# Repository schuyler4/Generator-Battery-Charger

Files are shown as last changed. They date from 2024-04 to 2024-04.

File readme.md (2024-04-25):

<h1> Generator Battery Charger </h1>
<p>
This is exactly what it sounds like, it is a generator that charges a lithium-ion battery pack. The difference
between this and a just plugging a battery charger into a generator (good luck finding a good HV battery charger off the
shelf) is the regulation is full system. That is, the constant current delivery to the battery is controlled via the
throttle on the engine.  
</p>
<h3>To What Extent Does this Actually Work?</h3>
<p>
A ~150V battery pack was charged for several minutes with the system, and it appeared to regulate current fairly well. A longer test
was not done because the battery pack was not fully protected with BMS (Cowboy Charging).  
There was not excessive current into the battery pack, but there was some ripple in the current (~0.5A), so the control system did not work
perfectly, but it did seem to behave more like a current source than a voltage source. Additionally, the battery pack was made out of
reused 18650 cells which may have had a higher than normal series resistance. This may have had an effect on the behavior of the control
system. 
</p>

See [Here](https://hackaday.io/project/195765-generator-battery-charger "here") for additional documentation
<h3> Directory Structure </h3>
<ul>
<li><b>circuit_board_designs:</b> This includes all the custom circuit board designs that were made for the project.</li>
<li><b>control_program:</b> This has several revisions of the firmware that controls the whole system. This firmware is run on an Arduino Nano.</li>
<li><b>mechanical:</b> Some 3D printed mechanical interface stuff.</li>
<li><b>pictures:</b> Pictures of the setup.</li>
<li><b>system:</b> This has schematic diagrams for both the HV powertrain and the low voltage system.</li>
<li><b>test:</b> Documentation of all the testing that was done with the system and various other component testing.</li>
</ul>

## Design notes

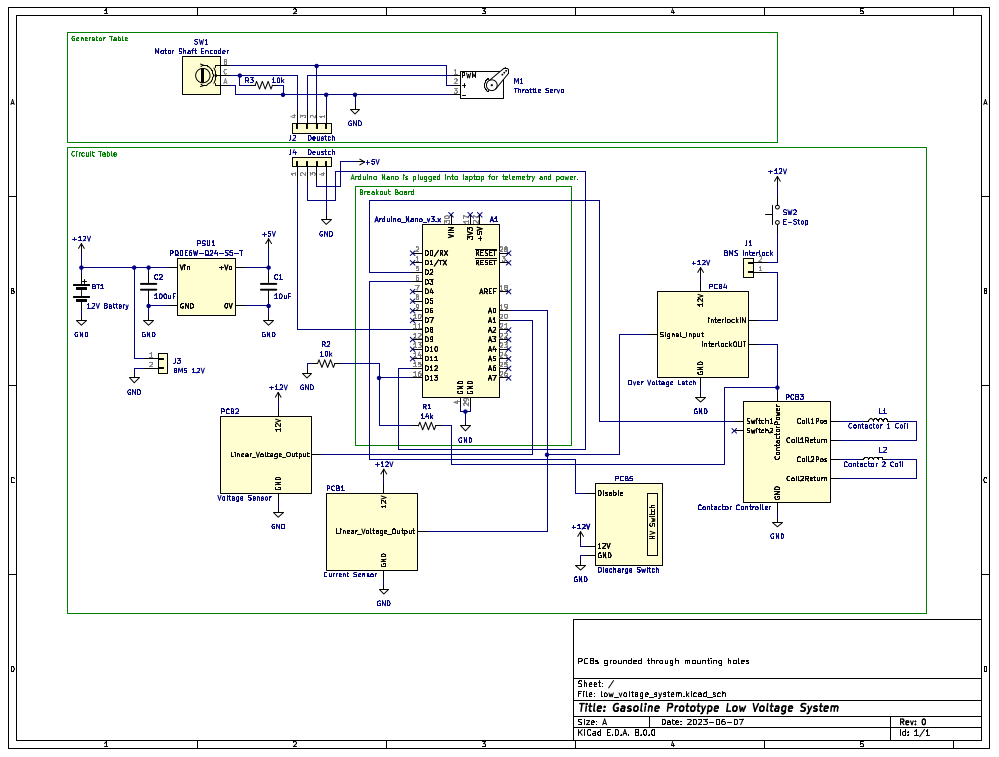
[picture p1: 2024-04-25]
pictures/low_voltage_schematic.png

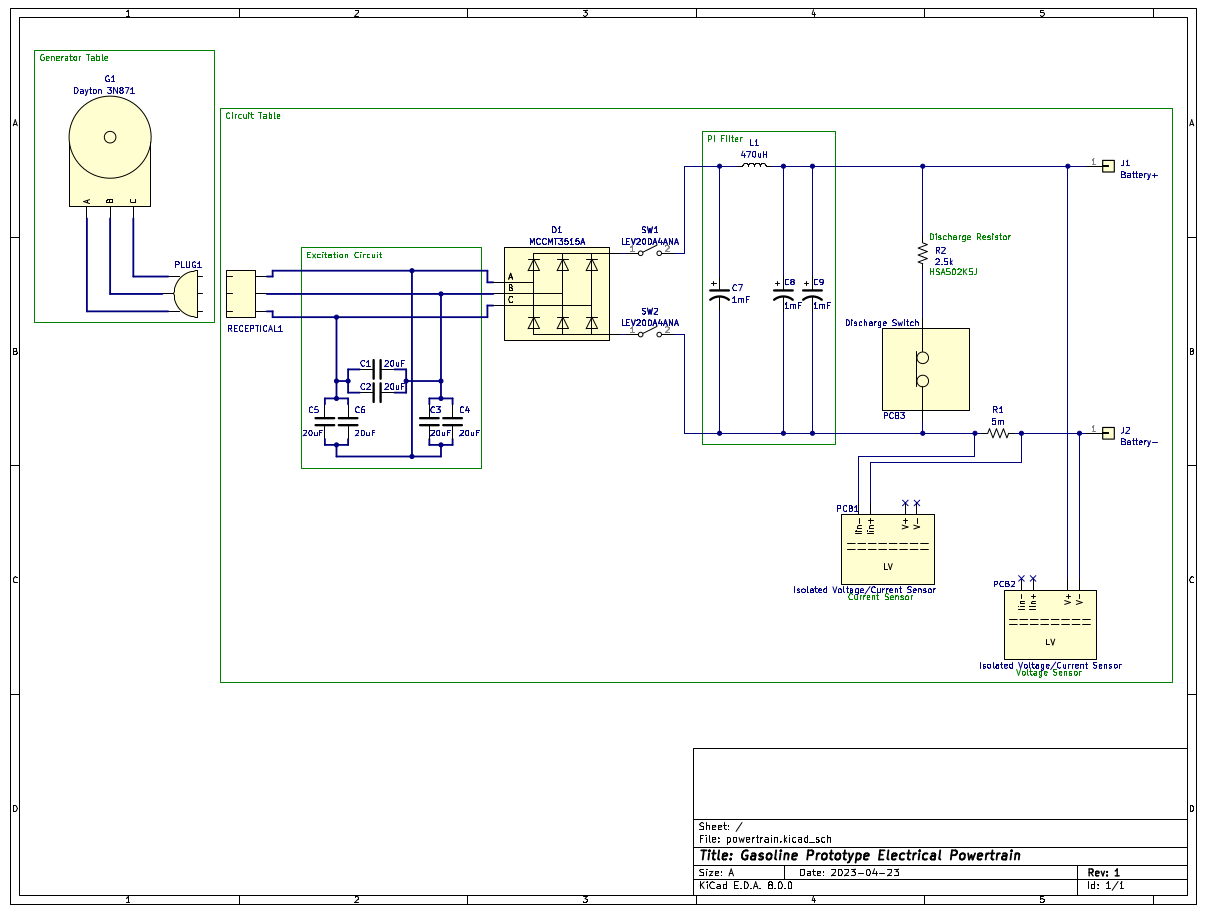
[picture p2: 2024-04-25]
pictures/powertrain_schematic.png

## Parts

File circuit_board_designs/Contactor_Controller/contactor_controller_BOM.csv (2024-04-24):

Item | Qty | Reference(s) | Value | Distributor | Distributor Part # | Unit Cost | Cost | Ordered
1 | 2 | D1, D2 | SK53A | Digikey | SK53A-LTPMSCT-ND | 0.36 | 0.72
2 | 2 | D3, D4 | SMF6.0A | Digikey | F5749CT-ND | 0.45 | 0.9
3 | 1 | J1 | Contactor Power | Digikey | 900-2125280200-ND | 1.13 | 1.13
4 | 1 | J3 | Contactor 1 Coil | Digikey | 900-2125280200-ND | 1.13 | 1.13
5 | 1 | J4 | Contactor 2 Coil | Digikey | 900-2125280200-ND | 1.13 | 1.13
6 | 1 | J5 | Switch 1 | Digikey | 900-2125280200-ND | 1.13 | 1.13
7 | 1 | J6 | Switch 2 | Digikey | 900-2125280200-ND | 1.13 | 1.13
8 | 2 | Q1, Q2 | DMG3418L | Digikey | DMG3418L-7DICT-ND | 0.43 | 0.86
9 | 2 | R1, R2 | 1k | Digikey | 311-1KMCT-ND | 0.1 | 0.2
10 | 2 | R3, R4 | 10k | Digikey | RNCP0805FTD10K0CT-ND | 0.1 | 0.2
 |  |  |  |  |  |  | 8.53

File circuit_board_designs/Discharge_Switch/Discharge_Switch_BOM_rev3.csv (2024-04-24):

Item | Qty | Reference(s) | Value | Manufacturer Part # | Distributor | Distributor Part # | Unit Cost | Cost | Carted
1 | 1 | D1 | 1N4148W | 1N4148W | Digikey | 1655-1N4148WCT-ND | 0.13 | 0.13
2 | 1 | D2 | SMF13A | SMF13A | Digikey | F5815CT-ND | 0.47 | 0.47
3 | 1 | D3 | SMF6.0A | SMF6.0A | Digikey | F5749CT-ND | 0.45 | 0.45
4 | 1 | J1 | Resistor | 212528-0200 | Digikey | 900-2125280200-ND | 1.13 | 1.13
5 | 1 | J2 | Return | 212528-0200 | Digikey | 900-2125280200-ND | 1.13 | 1.13
6 | 1 | J3 | 12V Power | 212528-0200 | Digikey | 900-2125280200-ND | 1.13 | 1.13
7 | 1 | J4 | Disable | 212528-0200 | Digikey | 900-2125280200-ND | 1.13 | 1.13
8 | 1 | K1 | DBR71205-HR | DBR71205-HR | Digikey | 725-DBR71205-HR-ND | 46.88 | 46.88
9 | 1 | Q1 | DMG3418L | DMG3418L-7 | Digikey | DMG3418L-7DICT-ND | 0.41 | 0.41
10 | 1 | R1 | 10k | RNCP0805FTD10K0 | Digikey | RNCP0805FTD10K0CT-ND | 0.1 | 0.1
11 | 1 | R2 | 1k | RNCP0805FTD1K00 | Digikey | RNCP0805FTD1K00CT-ND | 0.1 | 0.1
Total: |  |  |  |  |  |  |  | 53.06

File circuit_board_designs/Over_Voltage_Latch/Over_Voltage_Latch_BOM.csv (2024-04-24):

Item | Qty | Reference(s) | Value | Footprint | Manufacturer Part # | Distributor | Distributor Part # | Unit Cost | Cost | Carted
1 | 3 | C1, C2, C3 | 0.1uF | C_0805_2012Metric | 08055D104KAT2A | Digikey | 478-12790-1-ND | 0.1 | 0.3
2 | 1 | D1 | 1N4148W | D_SOD-123 | 1N4148W | Digikey | 1655-1N4148WCT-ND | 0.13 | 0.13
3 | 1 | D2 | SMF6.0A | D_SOD-123F | SMF6.0A | Digikey | F5749CT-ND | 0.45 | 0.45
4 | 1 | D3 | SMF13A | D_SOD-123F | SMF13A | Digikey | F5815CT-ND | 0.47 | 0.47
5 | 1 | J1 | 12V Power | MOLEX_2125280200 | 212528-0200 | Digikey | 900-2125280200-ND | 1.13 | 1.13
6 | 1 | J2 | Signal Input | MOLEX_2125280200 | 212528-0200 | Digikey | 900-2125280200-ND | 1.13 | 1.13
7 | 1 | J3 | Interlock Passthrough | MOLEX_2125280200 | 212528-0200 | Digikey | 900-2125280200-ND | 1.13 | 1.13
8 | 1 | K1 | G5Q-1A | Relay_SPST_Omron-G5Q-1A | G5Q-1A4 DC12 | Digikey | Z223-ND | 1.63 | 1.63
9 | 2 | R1, R4 | 1k | R_0805_2012Metric | RNCP0805FTD1K00 | Digikey | RNCP0805FTD1K00CT-ND | 0.1 | 0.2
10 | 4 | R3, R5, R6, R7 | 10k | R_0805_2012Metric | RNCP0805FTD10K0 | Digikey | RNCP0805FTD10K0CT-ND | 0.1 | 0.4
11 | 1 | RV1 | 10k | Potentiometer_Bourns_3266W | 3266W-1-103LF | Digikey | 3266W-103LF-ND | 4.2 | 4.2
12 | 1 | U1 | LM311 | SOIC-8_3.9x4.9mm_P1.27mm | LM311D | Digikey | 497-19620-ND | 0.67 | 0.67
13 | 1 | U2 | LM4040DBZ-2.5 | SOT-23 | LM4040C25FTA | Digikey | LM4040C25FCT-ND | 0.57 | 0.57
14 | 2 | TP1, TP2 | TestPoint | TestPointLoop_1.8mm | 1038 | Digikey | 36-1038-ND | 0.25 | 0.5
15 | 1 | U3 | NE555D | SOIC-8_3.9x4.9mm_P1.27mm | NE555DR | Digikey | 296-6501-1-ND | 0.44 | 0.44
Total: |  |  |  |  |  |  |  |  | 13.35

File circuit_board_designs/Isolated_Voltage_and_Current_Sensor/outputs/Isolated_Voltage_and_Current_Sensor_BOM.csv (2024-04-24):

Item | Qty | Reference(s) | Value | Manufacturer Part # | Mouser Part # | Unit Price | Price | Carted
1 | 1 | C1 | 1nF | CL21B102KBANFNC | 187-CL21B102KBANFNC | 0.1 | 0.1
2 | 7 | C2, C3, C4, C5, C6, C7, C10 | 0.1uF | 08055D104KAT2A | 581-08055D104K | 0.1 | 0.7
3 | 1 | C8 | 100pF | 0805B101M250CT | 791-0805B101M250CT | 0.1 | 0.1
4 | 1 | C9 | 2.2uF | CL21B225KOFNNNG | 187-CL21B225KOFNNNG | 0.12 | 0.12
5 | 1 | C11 | 10uF | CL21B106KOQNFNE | 187-CL21B106KOQNFNE | 0.23 | 0.23
6 | 2 | D1, D3 | SMF6.0A | SMF6.0A | 576-SMF6.0A | 0.46 | 0.92
7 | 1 | D2 | SMF13A | SMF13A | 637-SMF13A | 0.87 | 0.87
8 | 1 | F1 | 200mA | F0805B0R25FSTR | 581-F0805B0R25FSTR | 0.54 | 0.54
9 | 1 | J1 | Input HV | 212528-0200 | 538-212528-0200 | 0.88 | 0.88
10 | 1 | J2 | 12V Power | 212528-0200 | 538-212528-0200 | 0.88 | 0.88
11 | 1 | J3 | Linear Voltage Output | 212528-0200 | 538-212528-0200 | 0.88 | 0.88
12 | 1 | J4 | Input Current | 212528-0200 | 538-212528-0200 | 0.88 | 0.88
13 | 1 | PS1 | PDSE1-S12-S5-M | PDSE1-S12-S5-M | 490-PDSE1-S12-S5-M | 3.39 | 3.39
14 | 5 | R1, R15, R16, R13, R14 | 374k | CR0805-FX-3743ELF | 652-CR0805FX-3743ELF | 0.1 | 0.5
15 | 4 | R2, R10, R11, R12 | 100 | RMCF0805FT100R | 708-RMCF0805FT100R | 0.1 | 0.4
16 | 4 | R3, R4, R5, R6 | 1k | RMCF0805FT1K00 | 708-RMCF0805FT1K00 | 0.1 | 0.4
17 | 2 | R7, R8 | 15k | RMCF0805FT15K0 | 708-RMCF0805FT15K0 | 0.11 | 0.22
18 | 1 | U1 | AMC1100DUB | AMC1100DUB | 595-AMC1100DUB | 6.21 | 6.21
19 | 1 | U2 | L7805 | L7805ACD2T-TR | 511-L7805ACD2T-TR | 1.08 | 1.08
20 | 1 | U3 | OPA196xDBV | TS507CLT | 511-TS507CLT | 2.14 | 2.14
21 | 1 | R17 | 0 | CR0805AJ/-000EAS | 652-CR0805AJ/-000EAS | 0.1 | 0.1
total: |  |  |  |  |  |  | 21.54

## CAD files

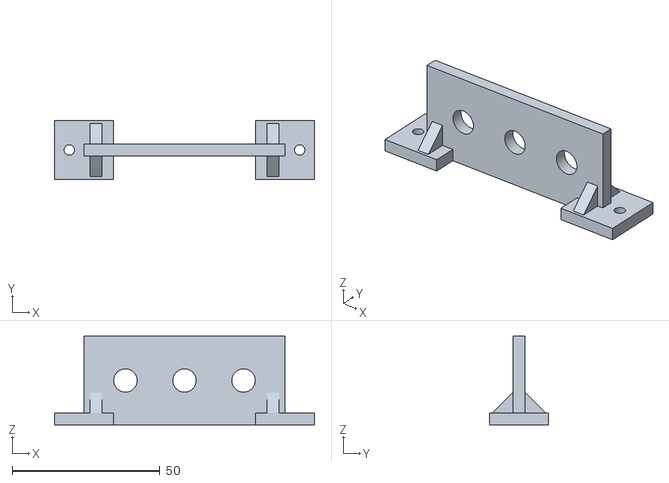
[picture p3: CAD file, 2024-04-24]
mechanical/phase_reciever/Phase_Reciever.stl
88.0 x 20.0 x 30.0

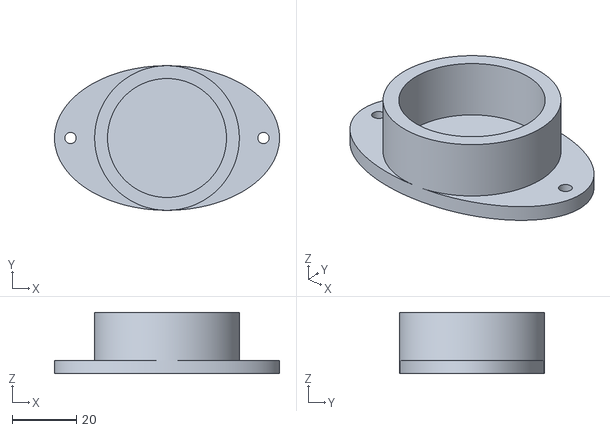
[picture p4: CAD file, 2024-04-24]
mechanical/pi_holder/inductor_holder.stl
70.0 x 45.0 x 19.0

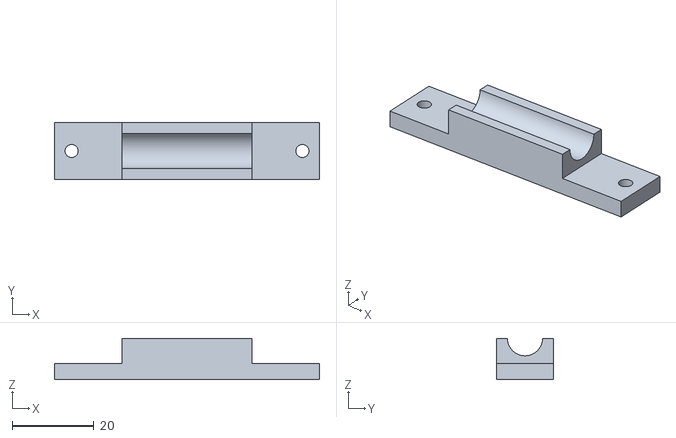
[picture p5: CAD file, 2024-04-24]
mechanical/shunt_holder/Shunt_Resistor_Holder_Bottom.stl
65.0 x 14.0 x 10.2

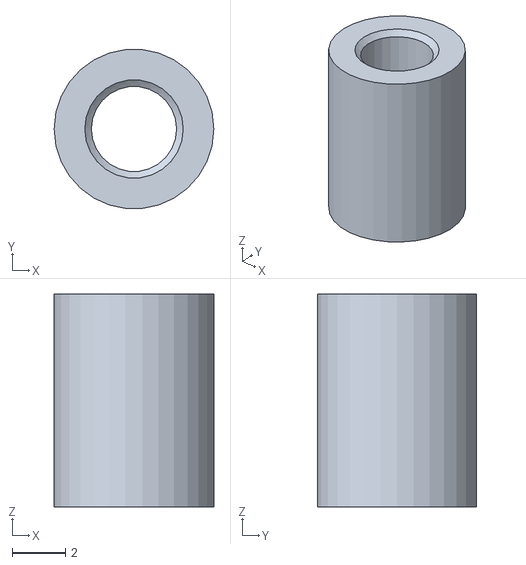
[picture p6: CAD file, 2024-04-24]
mechanical/stand_off/M3_stand_off-Body.stl
6.00 x 5.97 x 8.00

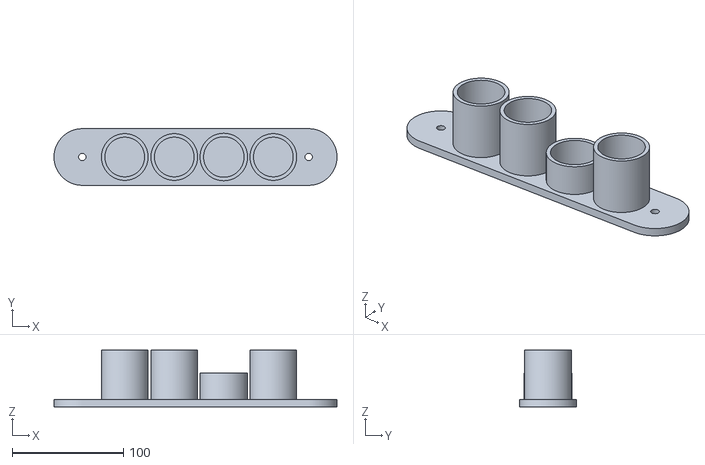
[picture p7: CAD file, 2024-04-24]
mechanical/pi_holder/PI_Holder.stl
254.0 x 50.8 x 50.8

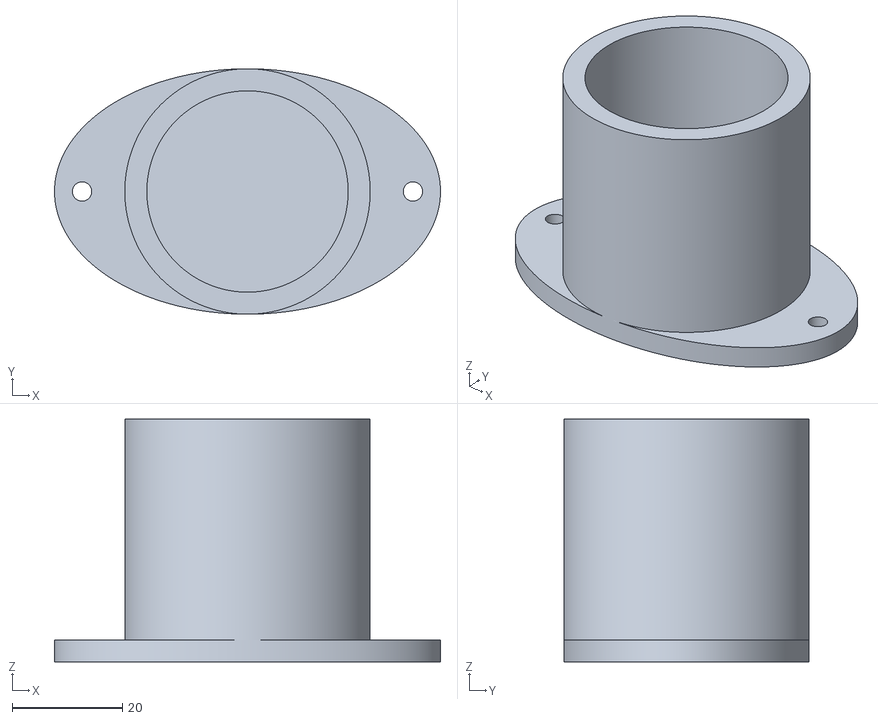
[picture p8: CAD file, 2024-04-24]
mechanical/pi_holder/capacitor_holder.stl
70.0 x 44.5 x 44.0

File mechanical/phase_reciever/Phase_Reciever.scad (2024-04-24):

module PhaseReciever()
{
    thickness = 4;
    width = 68;
    height = 30;
    
    hole_distance = 20;
    
    plug_hole_size = 7.9;
    
    curve_resolution=1000;
    
    fastener_hole_size = 3.5;
    
    foot_size = 20;
    
    gantrey_offset = 30;
    
    difference()
    {
        cube([width, thickness, height], center=true);
        
        for(i = [-1:1])
        {
            translate([i*hole_distance, 0, 0])
            rotate([90, 0, 0])
            cylinder(
                h=thickness+1, 
                center=true,
                d=plug_hole_size,
                $fn=curve_resolution);
        }
    }
    
    difference()
    {
        for(i = [-1:1])
        {
            if(i != 0)
            {
                translate([i*width/2, 0, -height/2 + 2])
                cube(
                    [foot_size, foot_size, thickness], 
                    center=true);
            }   
        }
        for(i = [-1:1])
        {
            if(i != 0)
            {
                translate([i*((width/2)+5), 0, -height/2 + 2])
                cylinder(
                    h=thickness+1, 
                    d=fastener_hole_size,
                    $fn=1000,
                    center=true);
            }
        }
    }  
    
    for(i = [-1:1])
    {
        if(i != 0)
        {
            translate([i*gantrey_offset,0,-2])
            rotate([-90,0,90])
            linear_extrude(height=thickness, center=true)
            polygon(points=[[0,0], [10,10], [0,10]]);
            
            translate([i*gantrey_offset,0,-2])
            rotate([-90,0,-90])
            linear_extrude(height=thickness, center=true)
            polygon(points=[[0,0], [10,10], [0,10]]);
        }
    }
}

PhaseReciever();

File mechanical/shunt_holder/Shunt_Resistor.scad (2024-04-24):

module ShuntResistor()
{
    cylinder_resolution = 1000;
    
    resistor_rotation = [90, 0, 0];
    resistor_length = 23.24;
    
    resistor_color = "SaddleBrown";
    
    lead_length = 10;
    lead_radius = 1.5;
    
    lead_color = "LightGrey";
    
    rotate(resistor_rotation)
    {
        color(resistor_color, 1.0)
        cylinder(
            h=resistor_length,
            r=4.17,
            center=true,
            $fn=cylinder_resolution );
        
        color(lead_color, 1.0)
        cylinder(
            h=resistor_length + 2*lead_length, 
            r=lead_radius, 
            center=true, 
            $fn=cylinder_resolution );
    }
}

     

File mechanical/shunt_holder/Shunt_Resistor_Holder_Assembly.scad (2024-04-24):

use <Shunt_Resistor.scad>
use <Shunt_Resistor_Holder_Bottom.scad>

rotate([0,0,90])
translate([0,0,8])
ShuntResistor();
ShuntResistorHolderBottom();

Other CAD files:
mechanical/shunt_holder/Shunt_Resistor_Holder_Bottom.scad

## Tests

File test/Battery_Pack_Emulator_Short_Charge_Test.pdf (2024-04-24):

Battery Pack Emulator Short Charge Test (7/27/2023)
Firmware Rev: 4
Purpose: This is the first charging test that is done with the battery pack emulator. The emulator contains 12 series cells that are monitored by a BMS as well as 36 reverse series zener diodes which are intended to emulate more cells. The voltage current characteristic of a zener diode should be similar to that of a battery that is sinking power. That is, approximately flat at a certain voltage, not linear like a resistor.
Description: The charger is set to a charge set point of 50. This corresponds to a current of 0.396A. The charger is set to this low of a current in an attempt to not burn up the zener diodes. The battery pack emulator is attached across the output of the charger and a short charge spurt is run.
Results: The charge test was terminated when some smoke was observed in the vicinity of the zener diodes. Hopefully, this was from the wood or electrical tape contacting the diodes and not the diodes themselves. The current through the battery emulator initially overshot at about 0.6A; however it then seemed to settle to about to about 0.34A to 0.38A. Before the test, the real 12s battery pack was measured at 37.93V. After the test this voltage rose to 38.35V. The following trace was recorded for the total voltage across the battery pack emulator.

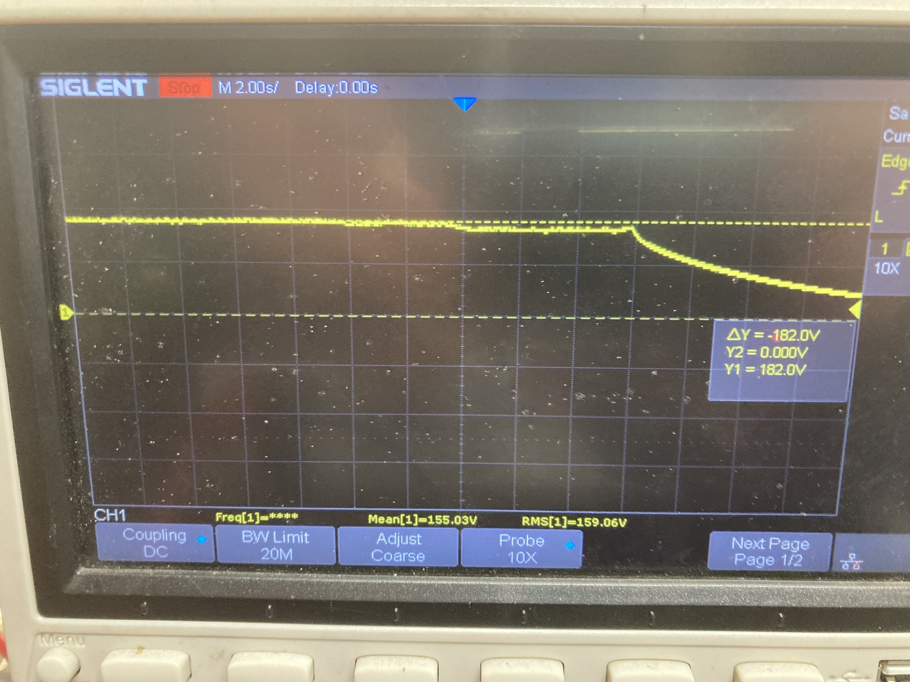
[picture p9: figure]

Analysis: The charge seemed to work as intended besides the smoke. As has been previously observed, the system does not maintain a perfect constant current. However, it regulates the current well enough to charge the batteries. That is, it acts more like a current source than a voltage source. The voltage per zener diode corresponds to approximately 4V which seems slightly high as the zener diodes are rated at 3.9V reverse voltage. This means that for future complete charge tests, the charge complete voltage threshold should be set at 193.2V or slightly lower.

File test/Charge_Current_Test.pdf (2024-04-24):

Charge Current Test (5/21/2023)
Firmware Rev: 3
Purpose: This test makes sure there are no excessive currents while charging and quantifies other charging current parameters.
Description: The test battery pack is charged with the charger system for two short spurts. During each charging spurt, the output signal of the current sensor is logged with an oscilloscope. Like the initial charge test, the test battery pack is being cowboy charged, so the pack cannot be charged for long. The parameters are found by using the horizontal cursors on the oscilloscope.
Results:
Parameter | Current Sensor Signal (V) | Measured Current (A)
Spurt 1 Average | 0.44 | 1.49
Spurt 1 Maximum | 0.56 | 1.9
Spurt 2 Average | 0.312 | 1.05
Spurt 2 Current Ripple | 0.128 | 0.42
Spurt 2 Maximum | 0.436 | 1.48
Spurt 2 Minimum | 0.164 | 0.54

Analysis: As has previously been observed, the system acts more like a constant current source than a constant voltage source; however, the current does tend to fluctuate. Additionally, a large amount of higher frequency ripple current is observed. It is possible that some of this ripple amplitude is due to noise.

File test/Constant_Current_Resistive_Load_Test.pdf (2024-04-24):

Constant Current Resistive Load Test (5/3/2023)
Purpose: Before attempting to charge a battery, it makes sense to test the constant current regulation ability of the generator charger system with a nonvolatile load.
Description: A control program is written that reads from the isolated current sensor and creates a feedback loop to regulate the current. A 250Ω load is attached across the output of the generator system, and the current set point is tested at several values. The theoretical current at the set point is calculated, and the actual current is measured using a hall effect multimeter.
Results:
ADC Code Set Point | Theoretical Current (A) | Measured Current (A) | Calculated Average Voltage (V)
120 | 0.98 | 1.04 | 260
100 | 0.815 | 0.87 | 217.5
75 | 0.605 | 0.74 | 185
An ADC set point of 50 was also attempted. This set point was not regulated in a stable manor. Analysis: The generator system seems to regulate with more stability and accuracy at higher voltages: approximately 150V-275V. The first test battery pack for charging should be in this voltage range.

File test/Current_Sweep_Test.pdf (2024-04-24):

Current Sweep Test (5/3/2023)
Purpose: This test is done to visualize and find the full range of current from the prototype generator into a 250 ohm load. It is also done to test the isolated voltage and current sensor when it is integrated into the system.
Description: First, the generator is brought to max RPM using the throttle servo control. The current is measured with the in-system current sensor and with a multimeter current sensor. Next, the generator is swept from min throttle to max throttle and the current is logged from the system current sensor and plotted using python. The data is logged using a serial transmission from the controller and Teraterm. Results:
Table 1: Comparison of in system current sensor to hall effect multimeter
Max Current Measured with in System Sensor (A) | Current Measured With Meter (A)
1.15 | 1.2

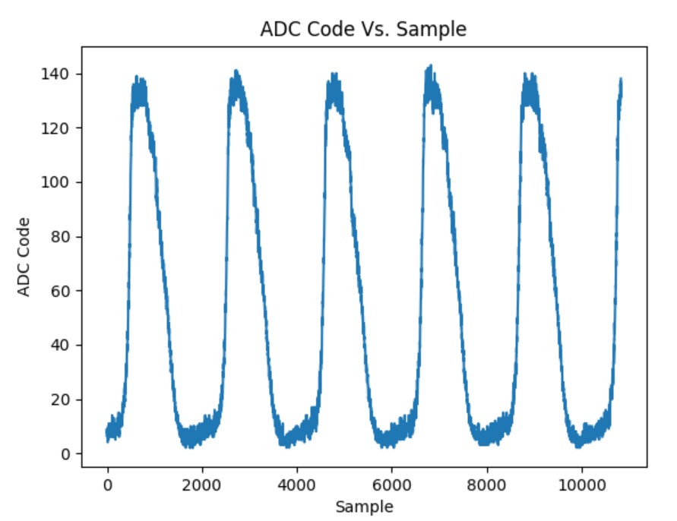
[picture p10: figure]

Figure 1: Plot of the ADC code over time

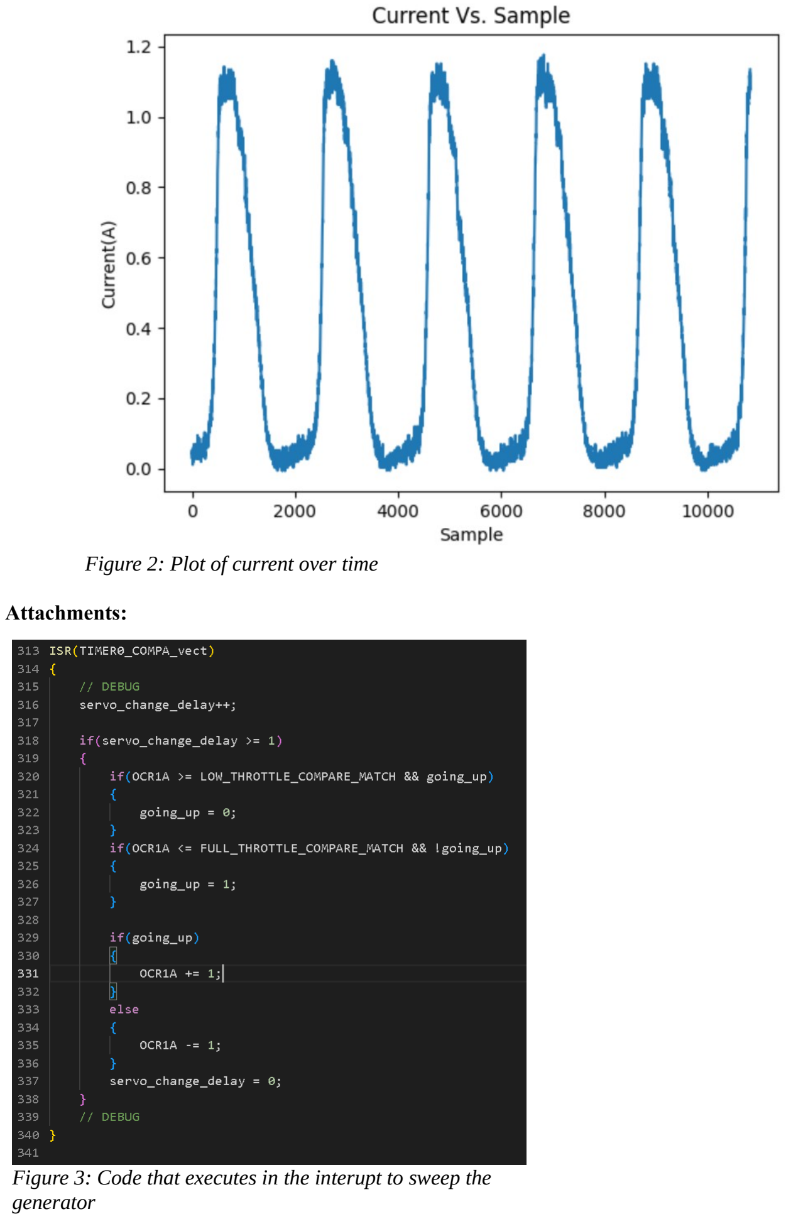
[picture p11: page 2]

Attachments:

Figure 3: Code that executes in the interupt to sweep the generator

Figure 2: Plot of current over time

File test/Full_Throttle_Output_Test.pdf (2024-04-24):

Full Throttle Output Test (7/19/2023)
Firmware Rev: 4
Purpose: This tests the maximum open circuit output voltage of the system, the accuracy of the voltage sensor, and the load regulation of the system.
Description: The system is put in full throttle test mode. This disables voltage control of the system and voltage level monitoring. Once in charge mode the open circuit output voltage is measured using an oscilloscope and the built in voltage sensor. Next, a 250Ω step load is applied and the voltage is measured using both methods again.
Results:

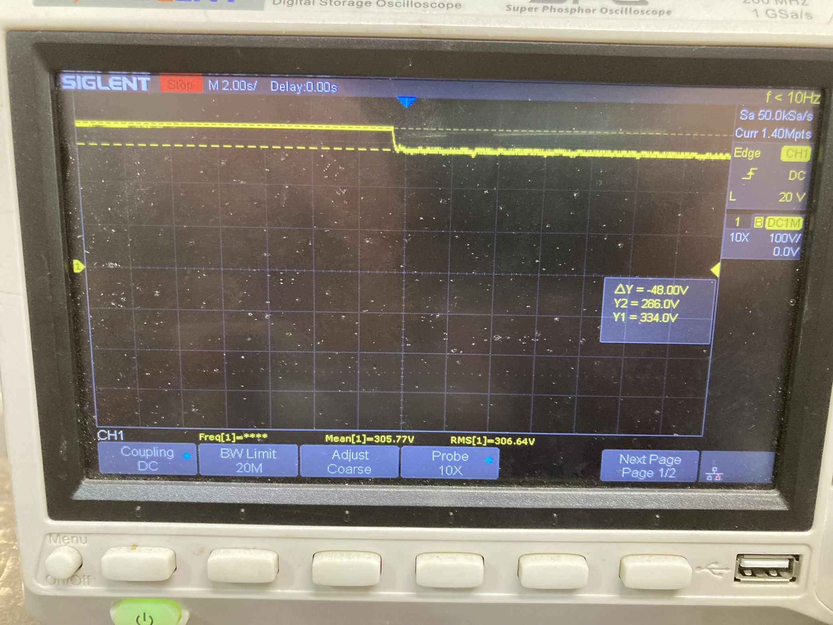
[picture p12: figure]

| Open Circuit | 250Ω Load
Oscilloscope (V) | 334 | 286
Voltage Sensor ADC Code | 472 | 408
Voltage Sensor (V) | 326.3 | 282.3
Error (%) | 2.3 | 1.3
The output power when the 250 ohm load is connected is 327W and the voltage drop when the 250Ω load is connected is 48V.
Analysis: The actual measured transfer function must be used to obtain an accurate result from the voltage sensor. That is, the theoretical transfer function cannot be used.

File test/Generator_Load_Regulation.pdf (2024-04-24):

Generator Load Regulation (5/4/2023)
Purpose: The purpose of this test is to see how much the output voltage of the generator varies just from changing the load.
Description: The induction generator with excitation capacitors is spun using a Dayton 6K748A motor. Presumably at around 3450RPM as this is the max RPM of the motor. Note that this is not necessarily a constant rotation source; it likely slows down as its load torque increases affecting the results of the test. Several resistive loads are attached across the output of the generator and the resulting output current and voltage is measured.
Results:
Load Resistance (Ω) | Current (A) | Output Voltage (V)
250 | 1.23 | 313
333 | 0.94 | 319.7
500 | 0.6 | 327
1000 | 0.3 | 332.5

Analysis: The output voltage seems to decrease approximately linearly with increaseing load current.

0.2 | 0.4 | 0.6 | 0.8 | 1 | 1.2 | 1.4

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
Output Voltage vs. Load Current

Output Voltage (V)

Current (A)

Output Voltage (V)

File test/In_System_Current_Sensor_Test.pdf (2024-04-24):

In System Current Sensor Test (5/15/2023)
Firmware Rev: 1
Purpose: The current sensor seemed to give wrong values on the last full system test. The current sensor should be tested while integrated into the system as much as possible.
Description: A power supply is attached across the shunt to supply a known current through it. The sensor output voltage is measured and recorded at various currents. Also at various currents, the ADC code that corresponds to the current that the system is reading is recorded. Both values are compared to their theoretical counterparts.
Results:
PSU Current(A) | Sensor Output Voltage (V) | Logged ADC Code
0.2 | 0.067 | 26
0.5 | 0.151 | 61
0.8 | 0.235 | 96
1 | 0.29 | 117
1.2 | 0.347 | 141
1.5 | 0.43 | 177
1.8 | 0.514 | 211
2 | 0.57 | 233
Theoretical Sensor Voltage (V) | Theoretical ADC Code | Sensor Error (%) | ADC Error (%)
0.06 | 24 | 11.67 | 8.33
0.15 | 61 | 0.67 | 0
0.24 | 98 | 2.08 | 2.04
0.3 | 122 | 3.33 | 4.1
0.36 | 147 | 3.61 | 4.08
0.45 | 184 | 4.44 | 3.8
0.54 | 221 | 4.81 | 4.52
0.6 | 245 | 5 | 4.9
0 | 0.5 | 1 | 1.5 | 2 | 2.5

0

0.1

0.2

0.3

0.4

0.5

0.6

Sensor Output Voltage Transfer Function

Sensor Output Voltage (V)

Current (A)

Sensor Output Voltage (V)

Analysis: The current sensor still seems to be functioning correctly in the system. Both the current sensor output, and the ADC code representing current that is read by the controller, seem to maintain linearity. For both parameters, the error is less than or equal to 5% except for the lowest value. The lowest value is not a usual current for the system, and the high error could also be due to the power supply sourcing the current.

0 | 0.5 | 1 | 1.5 | 2 | 2.5

0

50

100

150

200

250

ADC Code Transfer Function

Logged ADC Code

Current (A)

A

D

C

Code

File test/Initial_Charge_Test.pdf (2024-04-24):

Initial Charge Test (5/20/2023)
Firmware Rev: 3
Purpose: This is the first test where the generator system is used to put current through a battery pack to charge it.
Description: The test battery pack is attached across the output of the charger generator system. The current set point is 110. The generator is turned on, and the battery is charged. The battery pack voltage is logged using an oscilloscope, and a hall effect current sensor is also used to measure the current through the battery pack. Two short spurts of charging were done. The system is cowboy charging, so a long charging test cannot be done.
Results: The battery pack did not explode. The current that was read bounced around anywhere from 0.7A to 1A. The measured battery pack voltage before any charging took place was 151.6V, and the measured pack voltage after all the charging was 164.4V.

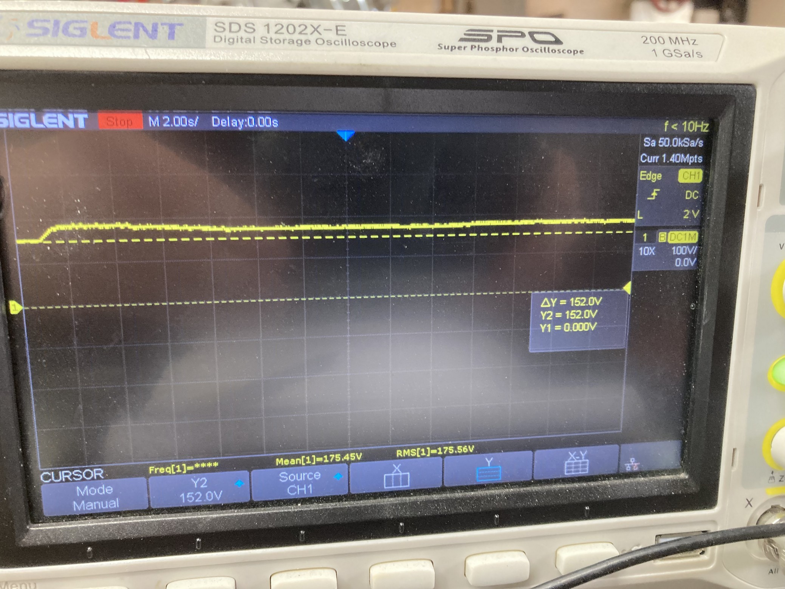
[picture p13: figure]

Figure 1: First Charging Spurt

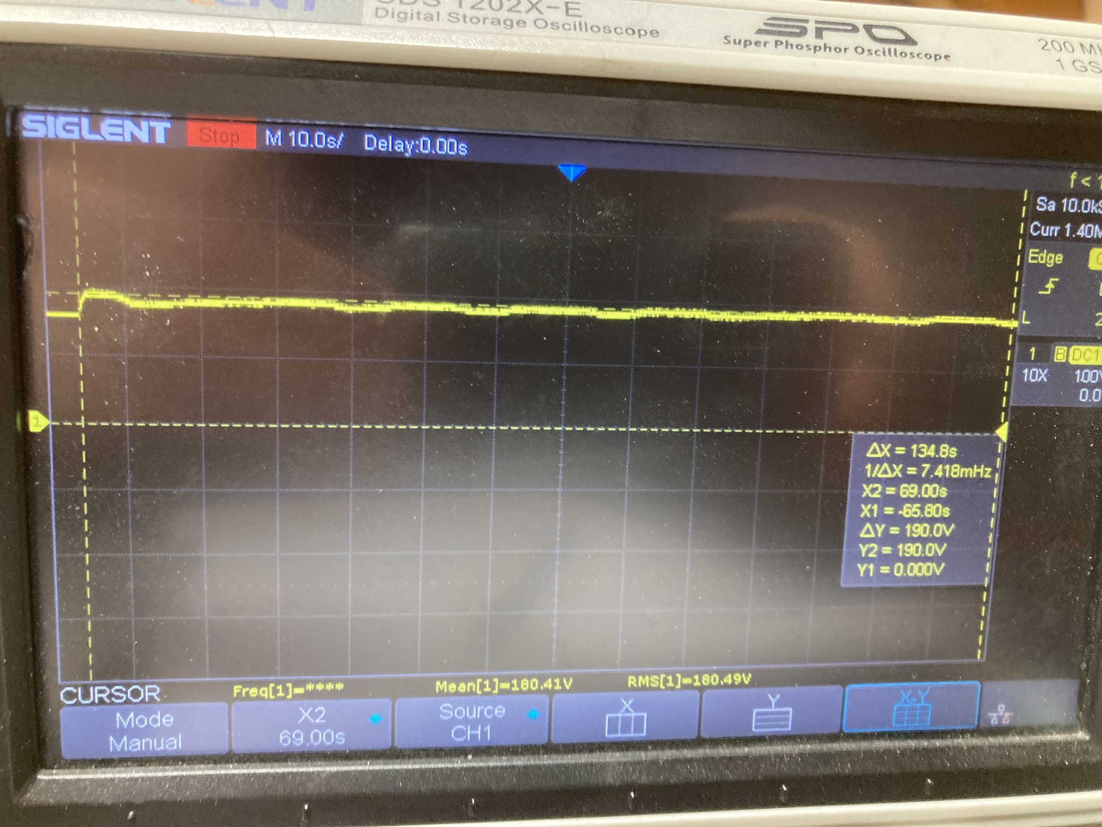
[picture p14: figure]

Analysis: The system does seem to be regulating the current to the extent required; however; the current is not completely constant and tends to bounce around. As has previously been observed, the battery voltage seems to increase more than normal at the start of charge. This is a possible indicator of poor cell health.

Figure 2: Second Charging Spurt

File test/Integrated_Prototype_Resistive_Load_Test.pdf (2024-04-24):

Integrated Prototype Resistive Load Test (7/19/2023)
Firmware Rev: 4
Purpose: This is a rerun of the resistive load test with all the electronics integrated into the prototype. The resistive load test verifies the control system can control a constant current without connecting a battery load.
Description: The charger is set to resistive load test mode. This allows the set point of the charger to be selected from three options. Each option is tested into a 250Ω resistive load. The current sensor measured ADC code is recorded and the current is also measured with a hall effect multimeter. Results:
ADC Code Set Point | Current Set Point (A)(1) | Measured ADC Code | Measured Current (A) | Calculated Voltage (V)(2)
120 | 0.983 | 119 | 0.96 | 240
100 | 0.816 | 101 | 0.83 | 207.5
75 | 0.606 | 73 | 0.65 | 162.5
(1) The current set point is computed using the current sensor transfer function.
(2) The voltage is calculated by multiplying the measured current by 250Ω.
Analysis: As was previously observed, the measured current seems to be closer to the set point for the higher voltage conditions.

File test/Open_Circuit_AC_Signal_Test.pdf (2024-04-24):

Open Circuit AC Signal Test (6/3/2023)
Purpose: This test quantifies the maximum frequency and voltage of the AC signals coming of the generator for analysis and component specifying.
Description: The generator is run with no load connected to the rectifier, with the engine set to full throttle. The voltage across each parallel set of generator excitation capacitors is measured with an oscilloscope. This measures the voltage of each phase.
Results:
Phase | Measured Peak Voltage(V) | RMS Voltage (V) | Frequency (Hz)
Phase 1 | 384 | 271.5 | 54.35
Phase 2 | 384 | 271.5 | 53.76
Phase 3 | 364 | 257.4 | 53.76
Analysis: Wiring and connectors that are used to couple these signals should be rated for at least 280VAC.
Attached Oscilloscope Captures:

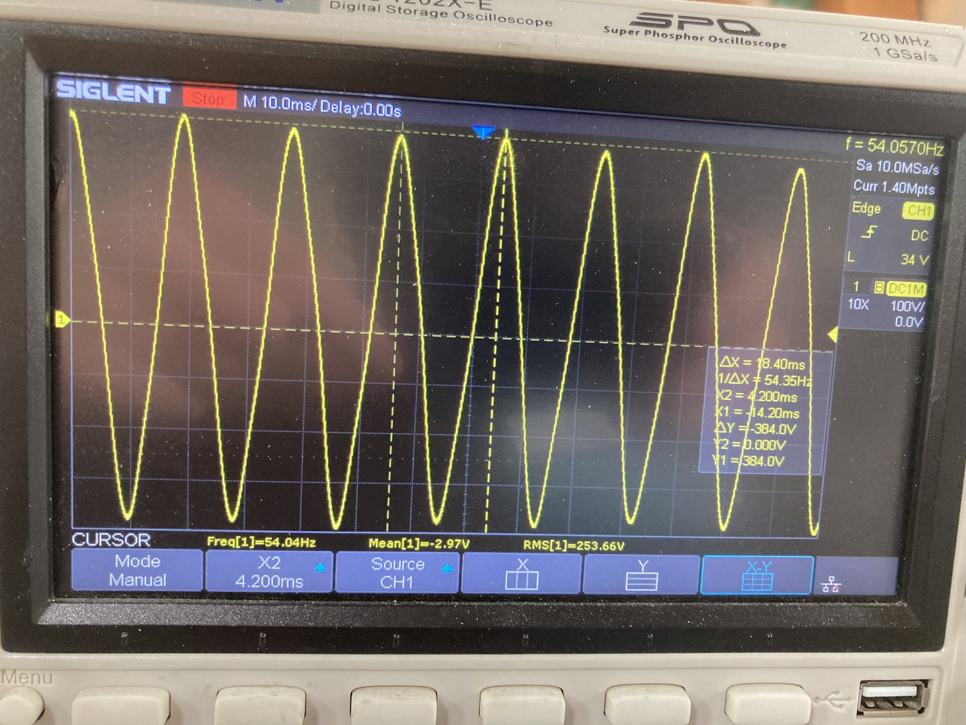
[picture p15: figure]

Figure 1: Phase 1

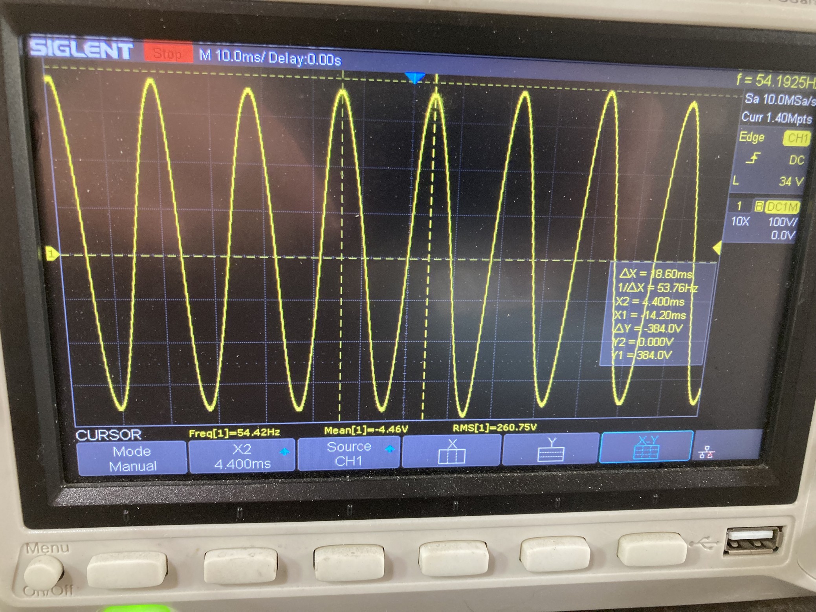
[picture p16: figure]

Figure 2: Phase2

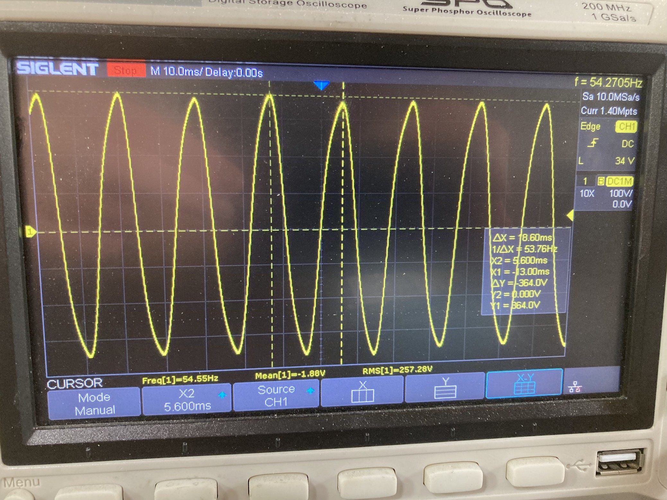
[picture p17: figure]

Figure 3: Phase3

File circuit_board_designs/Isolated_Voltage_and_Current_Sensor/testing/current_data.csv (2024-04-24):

Current (A) | Output Voltage(V)
0 | 0.01
0.5 | 0.156
1 | 0.296
1.5 | 0.447
2 | 0.586
2.5 | 0.739
3 | 0.88
3.5 | 1.023
4 | 1.167
4.5 | 1.308
5 | 1.467
5.5 | 1.604
6 | 1.754
6.5 | 1.893
7 | 2.046
7.5 | 2.184
8 | 2.337
8.5 | 2.492
9 | 2.63

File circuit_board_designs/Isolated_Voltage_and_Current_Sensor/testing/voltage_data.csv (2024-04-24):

Input (V) | Output (V)
0 | 0.01
4.967 | 0.026
10 | 0.042
15.23 | 0.058
20.07 | 0.073
25.05 | 0.089
30.08 | 0.105
338.5 | 1.077
33.52 | 0.117
100.5 | 0.309
161.7 | 0.517
194.2 | 0.629
232.9 | 0.744
259.9 | 0.824
318.2 | 1.014
290.7 | 0.927

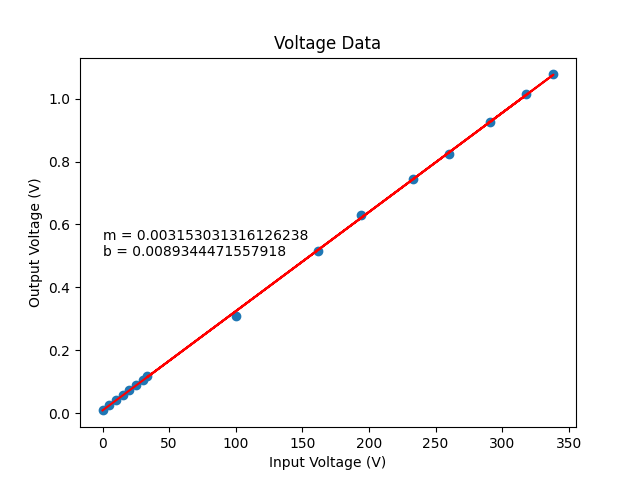
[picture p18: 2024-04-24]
circuit_board_designs/Isolated_Voltage_and_Current_Sensor/testing/plots/voltage_transfer_function.png

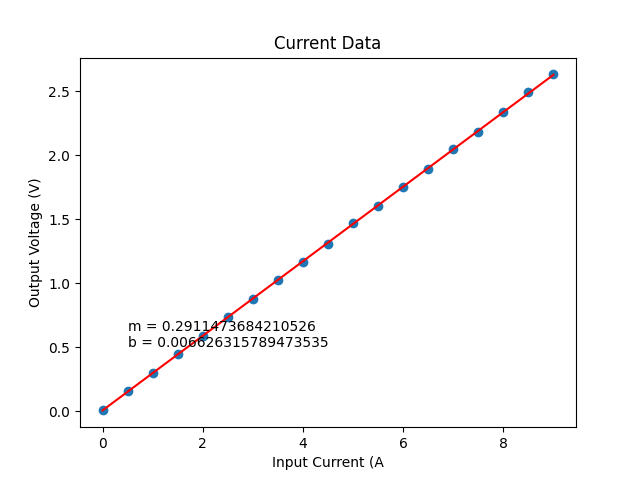
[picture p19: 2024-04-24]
circuit_board_designs/Isolated_Voltage_and_Current_Sensor/testing/plots/current_transfer_function.png

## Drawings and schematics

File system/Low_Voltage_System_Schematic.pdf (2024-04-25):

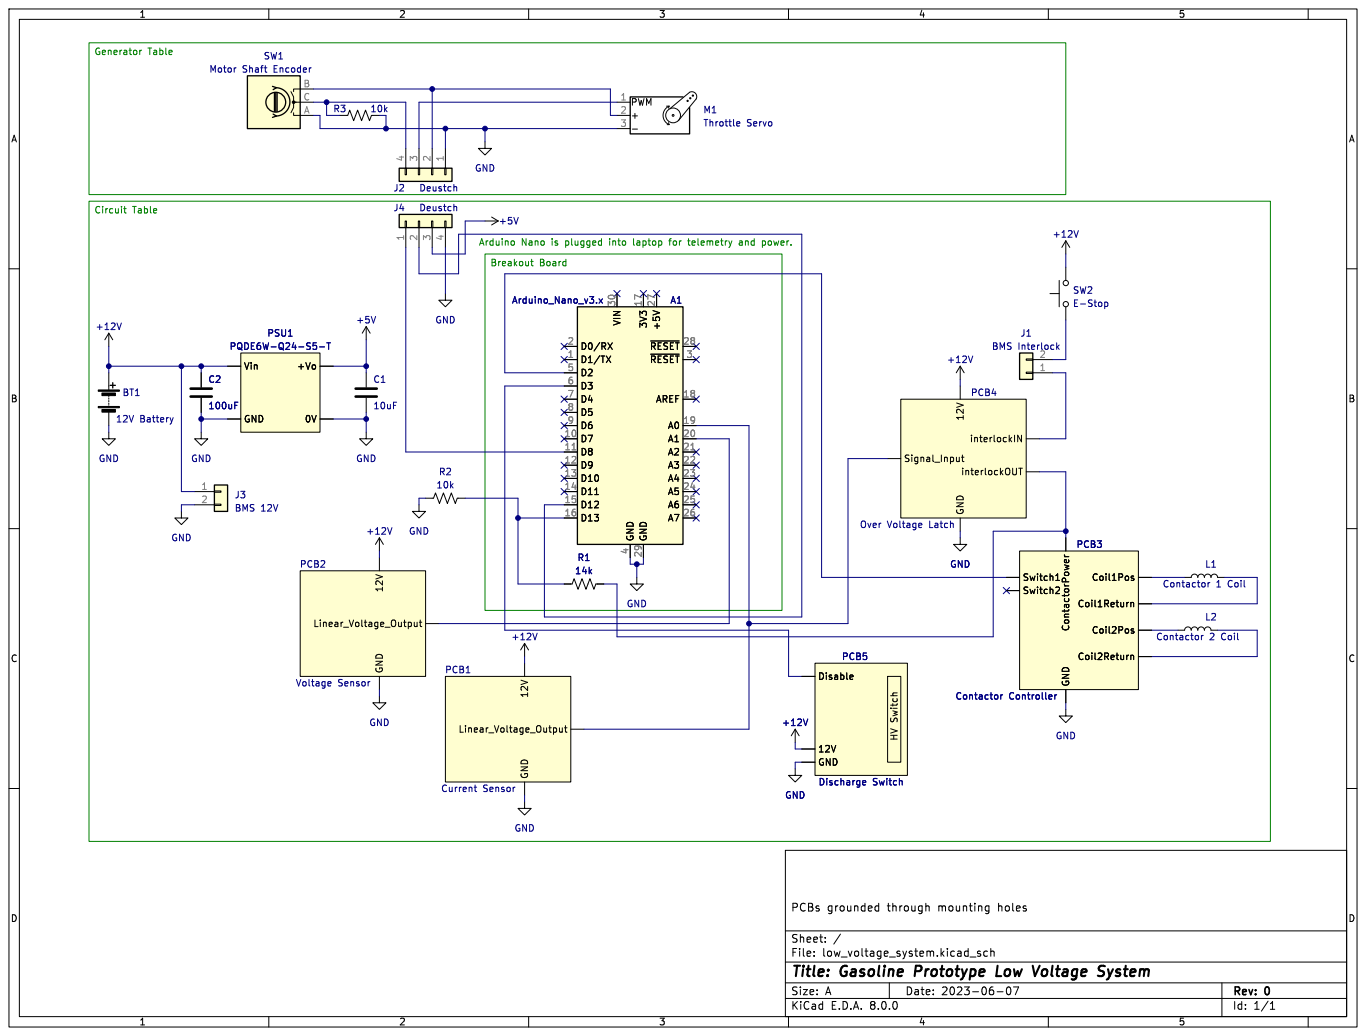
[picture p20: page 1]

interlockOUT PCB4 Over Voltage Latch +12V

Id: 1/1 Title: Gasoline Prototype Low Voltage System

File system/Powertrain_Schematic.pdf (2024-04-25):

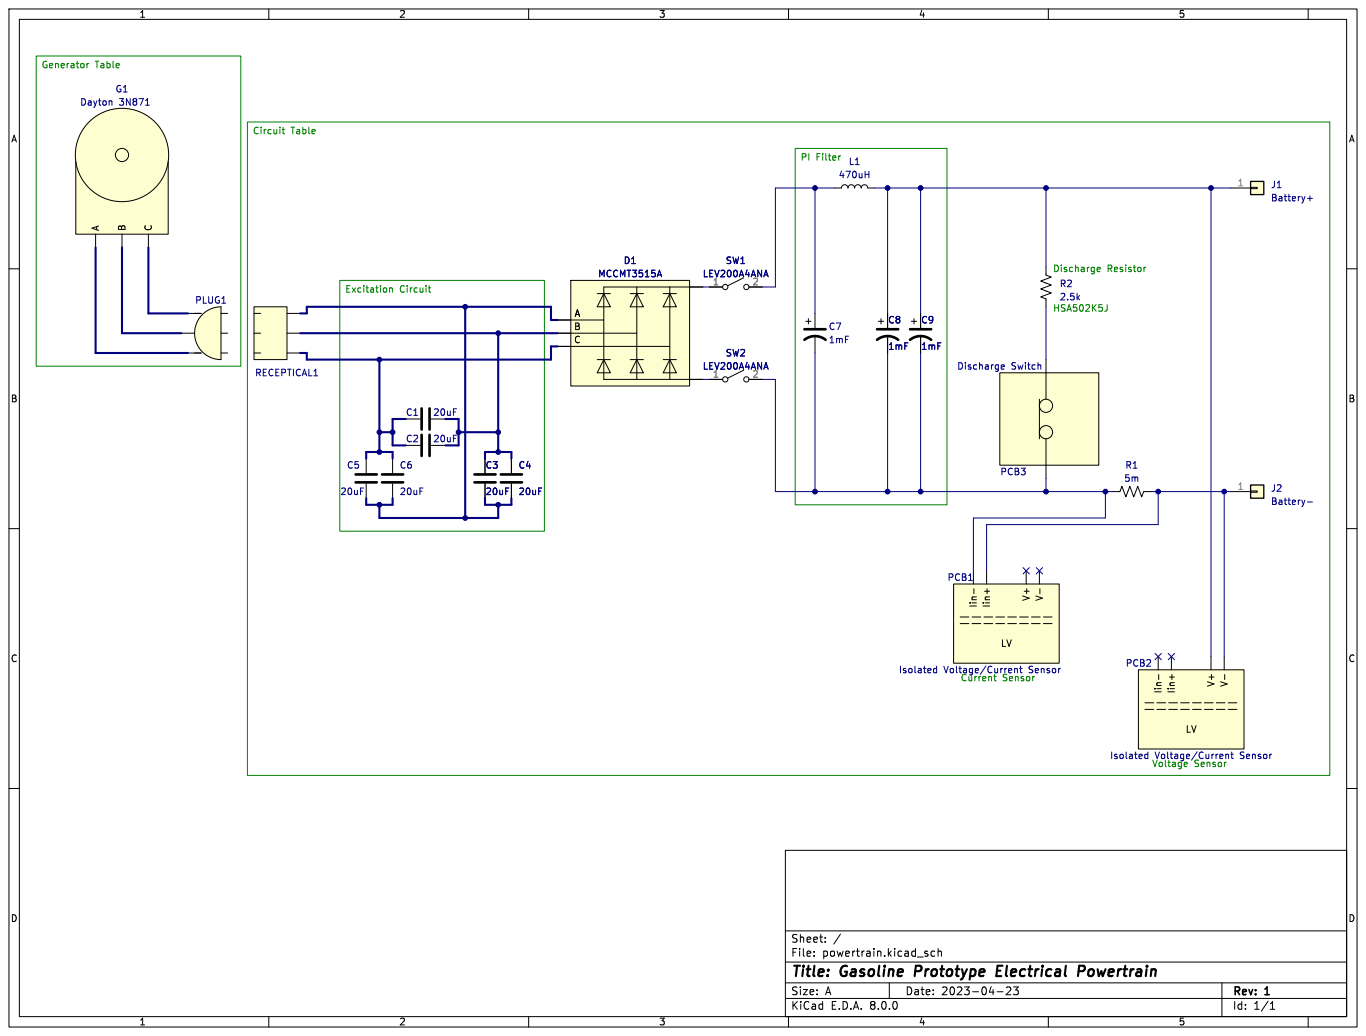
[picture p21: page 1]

20uF RECEPTICAL1 PLUG1

File: powertrain.kicad_sch Sheet: /
Id: 1/1 Title: Gasoline Prototype Electrical Powertrain

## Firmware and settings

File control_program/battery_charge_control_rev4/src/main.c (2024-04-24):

// 
// FILENAME: main.c
//
// Gasoline Generator Battery Charger Control Program 
//
// This program controls the generator battery charger prototype. 
// This involves controlling the throttle of a gasoline engine with a servo. 
// The gasoline engine is coupled to an induction generator which is connected 
// to an output rectifier. This whole system allows for voltage control simply
// by changing the throttle of the engine. A current measuring device is connected
// in series with the rectified and filtered output of the generator. This output is 
// then connected in series with the battery to charge. 
//
// The system also includes functionality for semi self testing. Given this, there is 
// also a user interface over UART to allow for the user to select the test they want to run 
// or just select the normal charge cycle.
//
// This program must read in the value from the current measuring device and adjust the
// throttle to maintain a constant current. In addition, it measures the RPM of the 
// generator using an encoder. 
//
// Written by Marek Newton
//

#define F_CPU 16000000UL

#include <avr/io.h>
#include <avr/interrupt.h>

#include "UART.h"
#include "running_average.h"
#include "RPM.h"
#include "logging.h"
#include "resistive_load_test.h"

#include "main.h"
  
// Constants for general byte manipulation.
#define BYTE_SIZE 8
#define BYTE_MASK 0xFF

// battery current reading parameters
#define CURRENT_FILTER_LENGTH 10
#define BATTERY_PACK_VOLTAGE_FILTER_LENGTH 10

// controller parameters
#define BATTERY_CURRENT_ADC_CODE_SET_POINT 50   
#define PROPORTIONAL_GAIN 0.001
#define MAX_CHARGE_VOLTAGE_ADC_CODE 500

// system state parameters
#define MINIMUM_ON_RPM 10
#define TOTAL_WARMUP_COUNT 2000
#define MAXIMUM_LOW_THROTTLE_RPM 200
#define MINIMUM_CHARGING_RPM 600

// full throttle time: 1.36ms
#define FULL_THROTTLE_COMPARE_MATCH 2775
// low throttle pulse time: 1.51ms
#define LOW_THROTTLE_COMPARE_MATCH 3020

// Command characters for the UART interface.
#define CHARGE_CYCLE_COMMAND '1'
#define CONTACTOR_CLOSE_TEST_COMMAND '2'
#define RESISTIVE_LOAD_TEST_COMMAND '3'
#define FULL_THROTTLE_TEST_COMMAND '4'

// this flag gets flipped when the ADC conversion is complete
static volatile unsigned int adc_complete_flag = 0;
// this flag gets flipped when the timer finishes
static volatile unsigned int control_timer_complete_flag = 0;
static volatile uint8_t rpm_timer_complete_flag = 0;

// this stores the ADC value
static volatile unsigned int adc_value;

// instantiate filter for adc current sampling
Running_Average_Filter current_adc_filter;

Charger_State charger_state;

Measurement_State measurement_state;

float compare_match_command = 0;
uint16_t warmup_count = 0;
int average_current_adc_value = 0;

uint16_t average_battery_pack_voltage_adc_value = 0;

uint16_t resistive_load_variable_set_point = 0;

uint16_t battery_current_set_point = 0;

RPM_meter my_rpm_meter;

// Setup the logging data structure.
Logging_Data my_logging_data;

// Instantiate the filter for battery pack voltage sampling.
Running_Average_Filter battery_pack_voltage_adc_filter;

System_State system_state;

int main(void)
{
    peripheral_setup();
    // start the first ADC conversion
    ADCSRA |= (1 << ADSC); 

    // set the length of the running average filter
    current_adc_filter.length = CURRENT_FILTER_LENGTH;
    battery_pack_voltage_adc_filter.length = BATTERY_PACK_VOLTAGE_FILTER_LENGTH;

    // Set the initial state to off.
    charger_state = OFF;

    // Set the initial measurement state to measure current.
    // This is basically an arbitrary choice.
    measurement_state = CURRENT_MEASUREMENT;

    log_startup(&my_logging_data);

    update_logging_data(
        &my_logging_data,
        charger_state,
        &my_rpm_meter,
        average_current_adc_value,
        average_battery_pack_voltage_adc_value,
        compare_match_command,
        warmup_count,
        battery_current_set_point
    );

    system_state = START_UP;

    start_up_sequence();

    set_current_set_point();

    // The loop below is for the charge cycle.
    while(1) // The program should never return.
    {
        set_discharge_circuit();
        // TODO: refactor this all into the ADC function
        if(adc_complete_flag)
        {
            // This executes after an ADC conversion has completed and the
            // flag has been set by the interupt.
            adc_complete(adc_value);
            adc_complete_flag = 0;
        }

        // interupt flag checks
        check_control_timer_complete();
        check_rpm_timer_complete(&my_rpm_meter);

        isolation_contactor_control();
    }

    return 1;
}

// Initial prompt for the user to choose the start up mode.
void start_up_sequence(void)
{
    // Log the initial start up menu.
    log_start_up_menu();
    // This loop is for the start up sequence.
    while(1)
    {
        char command_character = UART_getc();

        // Add an echo here.
        echo_selection(command_character);

        uint8_t enter_charge_loop = 0;

        switch(command_character)
        {
            case CHARGE_CYCLE_COMMAND:
                system_state = CHARGE_CYCLE;
                enter_charge_loop = 1;
                break;
            case CONTACTOR_CLOSE_TEST_COMMAND:
                contactor_close_test();
                break;
            case RESISTIVE_LOAD_TEST_COMMAND:
                system_state = RESISTIVE_LOAD_TEST;
                resistive_load_variable_set_point = get_variable_current_set_point();
                enter_charge_loop = 1;
                break;
            case FULL_THROTTLE_TEST_COMMAND:
                system_state = FULL_THROTTLE_TEST;
                enter_charge_loop = 1;
                break;
            default:
                // This is the case when the user enters an invalid command.
                log_invalid_command();
                log_start_up_menu();
                break;  
        }

        if(enter_charge_loop)
        {
            break;
        }
    }
}

// This calls all the setup functions.
void peripheral_setup(void)
{
    // disable interupts for setup
    cli(); 
    setup_IO();

    // call setup functions
    setup_servo_timer();
    setup_control_timer();
    setup_ADC();    
    setup_UART();

    // rpm setup
    setup_rpm_timer();
    setup_pin_change_interupt();

    // enable interupts
    sei();

    // initialize the rpm meter
    setup_rpm_meter(&my_rpm_meter);
}

// Set up the I/O pins as inputs or outputs.
void setup_IO(void)
{
    // Set the fault pin to an input.
    DDRB &= ~(1 << DDB4);
    // Set the fault pin to high impedance. 
    PORTB &= ~(1 << PORTB4);
    // Set discharge control to output. 
    DDRD |= (1 << DDD3);
    // Set pin D2 to an output to control the contactor. 
    DDRD |= (1 << DDD2);
}

// This function is called to run the contactor close test.
void contactor_close_test(void)
{
    PORTD |= (1 << PORTD2);
    log_contactor_close_test();
}

// This checks if there is an interlock loop fault.
void check_fault_input(void)
{
    if(!(PINB & (1 << PINB4)))
    {
        charger_state = FAULT;
    }
}

// This closes the isolation contactors when the system is charging. 
void isolation_contactor_control(void)
{
    if(charger_state == CHARGING)
    {
        PORTD |= (1 << PORTD2);
    }
    else
    {
        PORTD &= ~(1 << PORTD2);
    }
}

// Configure the ADC registers to setup an interupt ADC sample.
void setup_ADC(void)
{
    // set the ADC reference to the supply voltage (5V)
    ADMUX &= ~(1 << REFS0);
    ADMUX &= ~(1 << REFS1);

    // The 0th ADC channel is used initially, so the channel does not need 
    // to be configured.

    // enable the ADC
    // enable the ADC interupt
    ADCSRA = (1 << ADEN) | (1 << ADIE) | (1 << ADPS2) | (1 < ADPS1) | (1 << ADPS0);

    // disable digital logic on ADC pins
    DIDR0 |= (1 << ADC1D) | (1 << ADC0D); 
}

// Setup the timer that is used to time
// the sampling for the PID loop.
void setup_control_timer(void)
{
    // Set the timer to fcpu divide by 1024.
    TCCR0B |= (1 << CS02) | (1 << CS00);
    // Enable the compare match interupt.
    TIMSK0 |= (1 << OCIE0A);
    // Set the timer count for 10ms
    OCR0A = 156;
}

// Configure timer 1 for servo control.
void setup_servo_timer(void)
{
    // Set GPIO for timer1 output for OC1A and OC1B
    DDRB |= (1 << DDB1) | (1 << DDB2);
    // set entire TCCR1A register to 0
    TCCR1A = 0;
    // same for TCCR1B
    TCCR1B = 0;
    //initialize counter value to 0
    TCNT1  = 0;
    // top value
    ICR1 = 0xFFFF;
    // compare match value
    OCR1A = FULL_THROTTLE_COMPARE_MATCH;
    // set none-inverting mode
    TCCR1A |= (1 << COM1A1);
    // Fast PWM
    TCCR1A |= (1 << WGM11);
    TCCR1B |= (1 << WGM13) | (1 << WGM12);
    // Use eight as the prescaler
    TCCR1B |= (1 << CS11);
}

// Sets the current set point to the user selected or constant value depending if
// the system is in a test mode or not.
void set_current_set_point(void)
{
    if(system_state == RESISTIVE_LOAD_TEST)
    {
        battery_current_set_point = resistive_load_variable_set_point;
    }
    else
    {
        battery_current_set_point = BATTERY_CURRENT_ADC_CODE_SET_POINT;
    }
}

// This function executes when the ADC has finished its conversion.
void adc_complete(unsigned int adc_value)
{
    if(measurement_state == CURRENT_MEASUREMENT)
    {
        current_adc_filter.sample = adc_value;
        average_current_adc_value = running_average_filter_sample(&current_adc_filter);

        // Change to the voltage measurement state.
        measurement_state = VOLTAGE_MEASUREMENT;
    }
    else if(measurement_state == VOLTAGE_MEASUREMENT)
    {
        battery_pack_voltage_adc_filter.sample = adc_value;
        average_battery_pack_voltage_adc_value = running_average_filter_sample(&battery_pack_voltage_adc_filter);

        // Change to the current measurement state.
        measurement_state = CURRENT_MEASUREMENT;
    }

    // start another ADC conversion
    ADCSRA |= (1 << ADSC);
}

// This function checks if the control timer is complete, and 
// executes the control algorithm if the timer is complete.
void check_control_timer_complete(void)
{
    if(control_timer_complete_flag)
    {
        update_state_machine();

        update_logging_data(
            &my_logging_data,
            charger_state,
            &my_rpm_meter,
            average_current_adc_value,
            average_battery_pack_voltage_adc_value,
            compare_match_command,
            warmup_count,
            battery_current_set_point
        );

        periodic_logging(&my_logging_data);
        control_timer_complete_flag = 0;
    }
}

// This function handles the logic for turing on the discharge circuit. 
// This is dependent on if the system is in a charge mode or a self 
// test mode. 
void set_discharge_circuit(void)
{
    // Keep the discharge circuit on at all times except for 
    // when the system is in a charge cycle and is charging.
    // The discharge circuit is normally closed. 

    if(system_state == CHARGE_CYCLE || system_state == RESISTIVE_LOAD_TEST || system_state == FULL_THROTTLE_TEST)
    {
        if(charger_state == CHARGING)
        {
            PORTD |= (1 << PORTD3);
        }
        else
        {
            PORTD &= ~(1 << PORTD3);
        }
    }
    else
    {
        PORTD &= ~(1 << PORTD3);
    } 
}

// The implementation of the actual control algorithm that sets the charger
// to the correct output current. 
void control_charger(void)
{
    uint8_t range_min = LOW_THROTTLE_COMPARE_MATCH - compare_match_command >= FULL_THROTTLE_COMPARE_MATCH;
    uint8_t range_max = LOW_THROTTLE_COMPARE_MATCH - compare_match_command <= LOW_THROTTLE_COMPARE_MATCH;
    uint8_t in_rpm_range = my_rpm_meter.rpm > MINIMUM_CHARGING_RPM;

    if(range_min && average_current_adc_value < (float)battery_current_set_point)
    {
        compare_match_command += ((float)battery_current_set_point - average_current_adc_value)*PROPORTIONAL_GAIN;
    }
    else if(range_max && average_current_adc_value > (float)battery_current_set_point && in_rpm_range)
    {
        compare_match_command -= (average_current_adc_value - (float)battery_current_set_point)*PROPORTIONAL_GAIN;
    }
}

// This puts the system in an off state. 
void off(void)
{
    // Set the engine to maximum throttle so it can be turned on.
    OCR1A = FULL_THROTTLE_COMPARE_MATCH;
    warmup_count = 0;
    compare_match_command = 0;

    if(my_rpm_meter.rpm >= MINIMUM_ON_RPM)
    {
        charger_state = WARMING_UP;
    }
}

// This puts the system in a warming up state, which is necessary to warm up the engine. 
void warming_up(void)
{
    // Check if the state needs to be sent back to off.
    if(my_rpm_meter.rpm < MINIMUM_ON_RPM)
    {
        charger_state = OFF;
    }

    // The engine should be at full throttle to warm up.
    OCR1A = FULL_THROTTLE_COMPARE_MATCH;
    warmup_count++;

    // This checks for a state change to charging.
    if(warmup_count >= TOTAL_WARMUP_COUNT)
    {
        charger_state = THROTTLING_DOWN;
    }
}

void throttling_down(void)
{
    // Check if the state needs to be sent back to off.
    if(my_rpm_meter.rpm < MINIMUM_ON_RPM)
    {
        charger_state = OFF;
    }

    if(my_rpm_meter.rpm < MAXIMUM_LOW_THROTTLE_RPM)
    {
        charger_state = CHARGING;
    }

    OCR1A = LOW_THROTTLE_COMPARE_MATCH - 100;
}

void charging(void)
{
    // Check if the state needs to be sent back to off.
    if(my_rpm_meter.rpm < MINIMUM_ON_RPM)
    {
        charger_state = OFF;
    }

    if(system_state == FULL_THROTTLE_TEST)
    {
        // The charger is not controlled in the full throttle open circuit test. 
        OCR1A = FULL_THROTTLE_COMPARE_MATCH;
    }
    else
    {
        // Set the timer compare match to the controlled variable.
        OCR1A = LOW_THROTTLE_COMPARE_MATCH - ((int)compare_match_command);
        control_charger(); 
    }
}

// This function checks to see if the battery pack needs charging.
void check_charge_complete(void)
{
    if(average_battery_pack_voltage_adc_value >= MAX_CHARGE_VOLTAGE_ADC_CODE && system_state == CHARGE_CYCLE)
    {
        charger_state = CHARGE_COMPLETE;
    }
}

// Do different things in different states and call functions that change states.
void update_state_machine(void)
{
    check_fault_input();
    check_charge_complete();

    switch(charger_state)
    {
        case OFF:
            off();
            break;
        case WARMING_UP:
            warming_up();
            break;
        case THROTTLING_DOWN:
            throttling_down();
            break;
        case CHARGING: 
            charging();
            break;
        case FAULT:
            // Do nothing in the fault state.
            break;
        case CHARGE_COMPLETE:
            // Do nothing in the charge complete state.
            break;
        default:
            // The system can't not have a state.
            break; // do nothing
    }   
}

// This ISR is called when the ADC completes a conversion.
ISR(ADC_vect)
{
    // read the integer result from the ADC result register
    adc_value = ADC;

    // Change the ADC channel based on the last measurement.
    if(measurement_state == CURRENT_MEASUREMENT)
    {
        ADMUX |= (1 << MUX0);
    }
    else if(measurement_state == VOLTAGE_MEASUREMENT)
    {
        ADMUX &= ~(1 << MUX0);
    }

    // This flag executes the ADC finished function in main.
    adc_complete_flag = 1;
}

// This ISR is called when the control timer is done.
ISR(TIMER0_COMPA_vect)
{
    // Reset the control timer.
    TCNT0 = 0;
    // Set the timer complete flag.
    control_timer_complete_flag = 1;
}

// This ISR is called when the RPM timer is done.
ISR(TIMER2_COMPA_vect)
{
    // Reset the RPM timer.
    TCNT2 = 0;
    // Set the timer complete flag.
    set_rpm_timer_flag(&my_rpm_meter);
}

// Increment the number of counts received from the encoder.
ISR(PCINT0_vect)
{
    // Check to make sure the pin change is a rising edge.
    if(PINB & (1 << PINB0))
    {
        increment_encoder_counts(&my_rpm_meter);
    }
}

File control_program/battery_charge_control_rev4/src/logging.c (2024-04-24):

//
//      FILENAME: logging.c
//
// description: This file takes care of all the logging for
// the program. Logging entails sending data over UART so
// the user can read it with a serial monitor. All important
// info about the charger should be logged. 
//
// Written by Marek Newton
//

#include "main.h"
#include "UART.h"
#include "RPM.h"

#include "logging.h"

#define SEND_COMMAND "SEND A COMMAND"
#define CHARGE_COMMAND "1 - CHARGE"
#define CONTACTOR_TEST "2 - CONTACTOR TEST"
#define RESISTIVE_LOAD_TEST "3 - RESISTIVE LOAD TEST"
#define FULL_THROTTLE_OPEN_CIRCUIT_TEST "4 - FULL THROTTLE OPEN CIRCUIT TEST"

#define ADC_CODE_SELECTION_MESSAGE "Select a current ADC code set point for the resistive load test: "
#define FIRST_SET_POINT "1 - 120"
#define SECOND_SET_POINT "2 - 100"
#define THIRD_SET_POINT "3 - 75"

#define ECHO_MESSAGE "You entered: "

#define CONTACTOR_TEST_MESSAGE "Verify that the contactors have closed."

#define RESISTIVE_LOAD_TEST_MESSAGE "Enter a current set point: "

#define INVALID_COMMAND_MESSAGE "Invalid command, try again."

#define SYSTEM_DATA_HEADER "== SYSTEM DATA =="

#define STATE_STRING "Charger State: "
#define OFF_STRING "OFF"
#define WARMING_UP_STRING "WARMING UP"
#define THROTTLING_DOWN_STRING "THROTTLING DOWN"
#define CHARGING_STRING "CHARGING"
#define FAULT_STRING "FAULT"
#define CHARGE_COMPLETE_STRING "CHARGE COMPLETE"

#define STARTUP_MESSAGE "GENERATOR CHARGER CONTROLLER RESET"

#define RPM_STRING "RPM: "
#define CURRENT_ADC_CODE_STRING "CURRENT ADC CODE: "
#define VOLTAGE_ADC_CODE_STRING "VOLTAGE ADC CODE: "
#define CONTROLLED_COMMAND_STRING "CONTROLLED_COMMAND: "
#define WARMUP_COUNT "WARMUP COUNT: "
#define CURRENT_SET_POINT_STRING "CURRENT SET POINT: "

#define NEWLINE_AND_CARRIAGE_RETURN "\n\r"
#define LOGGING_COUNT_DELAY 100

// The static functions go first.

// This function logs the current state that 
// the charger is in. 
static void log_state(Charger_State state)
{
    UART_transmit_string(STATE_STRING);

    switch(state)
    {
        case OFF:
            UART_transmit_string(OFF_STRING);
            break;
        case WARMING_UP:
            UART_transmit_string(WARMING_UP_STRING);
            break;
        case THROTTLING_DOWN:
            UART_transmit_string(THROTTLING_DOWN_STRING);
            break;
        case CHARGING:
            UART_transmit_string(CHARGING_STRING);   
            break;
        case FAULT:
            UART_transmit_string(FAULT_STRING);
            break;
        case CHARGE_COMPLETE:
            UART_transmit_string(CHARGE_COMPLETE_STRING);
            break;  
        default:
            // do nothing
            break;
    }

    UART_transmit_string(NEWLINE_AND_CARRIAGE_RETURN);
}

// This function logs all the measured values that
// are important to the operation of the charger.
static void log_measurements(Logging_Data *logging_data_pointer)
{
    UART_transmit_string(SYSTEM_DATA_HEADER);
    UART_transmit_string(NEWLINE_AND_CARRIAGE_RETURN);

    // Only show the warmup count, if the system is, 
    // in fact, warming up.
    if(logging_data_pointer->state == WARMING_UP)
    {
        UART_transmit_string(WARMUP_COUNT);
        UART_transmit_int(logging_data_pointer->warmup_count);
        UART_transmit_string(NEWLINE_AND_CARRIAGE_RETURN);
    }

    log_state(logging_data_pointer->state);

    // Log the RPM.
    UART_transmit_string(RPM_STRING);
    UART_transmit_int(logging_data_pointer->rpm_meter->rpm);
    UART_transmit_string(NEWLINE_AND_CARRIAGE_RETURN);

    // Log the measured current ADC code.
    UART_transmit_string(CURRENT_ADC_CODE_STRING);
    UART_transmit_int(logging_data_pointer->averaged_current_adc_code);
    UART_transmit_string(NEWLINE_AND_CARRIAGE_RETURN);

    // Log the measured voltage ADC code.
    UART_transmit_string(VOLTAGE_ADC_CODE_STRING);
    UART_transmit_int(logging_data_pointer->voltage_adc_code);
    UART_transmit_string(NEWLINE_AND_CARRIAGE_RETURN);

    // Log the control command.
    UART_transmit_string(CONTROLLED_COMMAND_STRING);
    UART_transmit_int((int)logging_data_pointer->controlled_command);
    UART_transmit_string(NEWLINE_AND_CARRIAGE_RETURN);

    // Log the current set point. 
    UART_transmit_string(CURRENT_SET_POINT_STRING);
    UART_transmit_int(logging_data_pointer->current_set_point);
    UART_transmit_string(NEWLINE_AND_CARRIAGE_RETURN);

    // This adds some white space to the end of the log.
    UART_transmit_string(NEWLINE_AND_CARRIAGE_RETURN);
    UART_transmit_string(NEWLINE_AND_CARRIAGE_RETURN);
}

void update_logging_data(
    Logging_Data* logging_data_pointer,
    Charger_State state,
    RPM_meter *rpm_meter,
    int averaged_current_adc_code,
    uint16_t voltage_adc_code,
    float controlled_command,
    uint16_t warmup_count,
    uint16_t current_set_point
    )
{
    logging_data_pointer->state = state;
    logging_data_pointer->rpm_meter = rpm_meter;
    logging_data_pointer->averaged_current_adc_code = averaged_current_adc_code;
    logging_data_pointer->voltage_adc_code = voltage_adc_code;
    logging_data_pointer->controlled_command = controlled_command;
    logging_data_pointer->warmup_count = warmup_count;
    logging_data_pointer->current_set_point = current_set_point;
}

// This function is called at the beginning of the program.
void log_startup(Logging_Data *logging_data_pointer)
{
    // Initialize the logging count to zero.
    logging_data_pointer->logging_count = 0;

    UART_transmit_string(STARTUP_MESSAGE);
    UART_transmit_string(NEWLINE_AND_CARRIAGE_RETURN);
    // Add some whitespace.
    UART_transmit_string(NEWLINE_AND_CARRIAGE_RETURN);
}

// This function should be called in the control loop 
// to log the data occasionally. 
void periodic_logging(Logging_Data* logging_data_pointer)
{
    if(logging_data_pointer->logging_count >= LOGGING_COUNT_DELAY)
    {
        log_measurements(logging_data_pointer);

        // reset the count
        logging_data_pointer->logging_count = 0;
    }
    else
    {
        logging_data_pointer->logging_count++;
    }
}

// Sends all the messages necessary for the initial start up menu.
void log_start_up_menu(void)
{
    UART_transmit_string(SEND_COMMAND);
    UART_transmit_string(NEWLINE_AND_CARRIAGE_RETURN);

    UART_transmit_string(CHARGE_COMMAND);
    UART_transmit_string(NEWLINE_AND_CARRIAGE_RETURN);

    UART_transmit_string(CONTACTOR_TEST);
    UART_transmit_string(NEWLINE_AND_CARRIAGE_RETURN);

    UART_transmit_string(RESISTIVE_LOAD_TEST);
    UART_transmit_string(NEWLINE_AND_CARRIAGE_RETURN);

    UART_transmit_string(FULL_THROTTLE_OPEN_CIRCUIT_TEST);
    UART_transmit_string(NEWLINE_AND_CARRIAGE_RETURN);
}

void log_contactor_close_test(void)
{
    UART_transmit_string(CONTACTOR_TEST_MESSAGE);
}
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
